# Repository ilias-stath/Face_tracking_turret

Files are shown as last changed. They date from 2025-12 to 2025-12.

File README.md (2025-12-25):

# Face_tracking_turret
## Overview
This is a project created for the course Embedded Systems of the University of Western Macedonia. The system is based on the PoseNet deep learning model and is designed to track human faces that appear on the frame and follow the closest one autonomously. The turret can rotate continuously on its vertical Z-axis and tilt up to 75° on the horizontal Y-axis, allowing precise targeting. By moving the camera both on Z and Y, it creates a closed-loop control system that eliminates the need for encoders in the motors. It also corrects rotational errors using a PID conroller. Distance estimation for face switching is done by measuring face size in video frames rather than using depth sensing, which, while potentially less reliable, proved effective in testing.
<br><br><br>
There are expicit instructions for the hardware and software in the files attached.

turret_picture_front_close
turret_picture_side
turret_working_video

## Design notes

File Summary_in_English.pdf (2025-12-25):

The project is a semester assignment developed for the Embedded Systems course, under the supervision of Dr. Minas Dasygenis. The system is based on the PoseNet deep learning model and is designed to track and follow human faces autonomously. The turret can rotate continuously on its vertical Z-axis and tilt up to 75° on the horizontal Y- axis, allowing precise targeting. By moving the camera both on Z and Y

rotations, it creates a closed-loop control system that eliminates the need for encoders in the motors and corrects rotational errors using controllers like PID. Distance estimation for face switching is done by measuring face size in video frames rather than using depth sensing, which, while potentially less reliable, proved effective in testing. The hardware includes the stepper motor 42BYGHW804 of the wantai

stepper motors, along the A4988 stepper driver, for Z-axis rotation and the high-torque HS-645MG servo from Hitex for the Y-axis. Both are controlled via an Arduino Nano CH340. Video capture is handled by the Creative BlasterX Senz3D camera, although its depth features were not used due to driver limitations. A Google Coral Dev Board with Edge TPU accelerates the PoseNet model in real-time, offering fast and reliable facial tracking. The system is powered by two separate sources: a power bank for the Coral and a NiMH battery pack for the motors. Software- wise, the movement scripts are written in Arduino IDE, utilizing libraries

such as, Servo and A4988, and the face recognition script is written in python, enhancing the already existing script pose_camera.py made by Posenet. The overall system integrates motion control, computer vision, and machine learning in a compact platform.

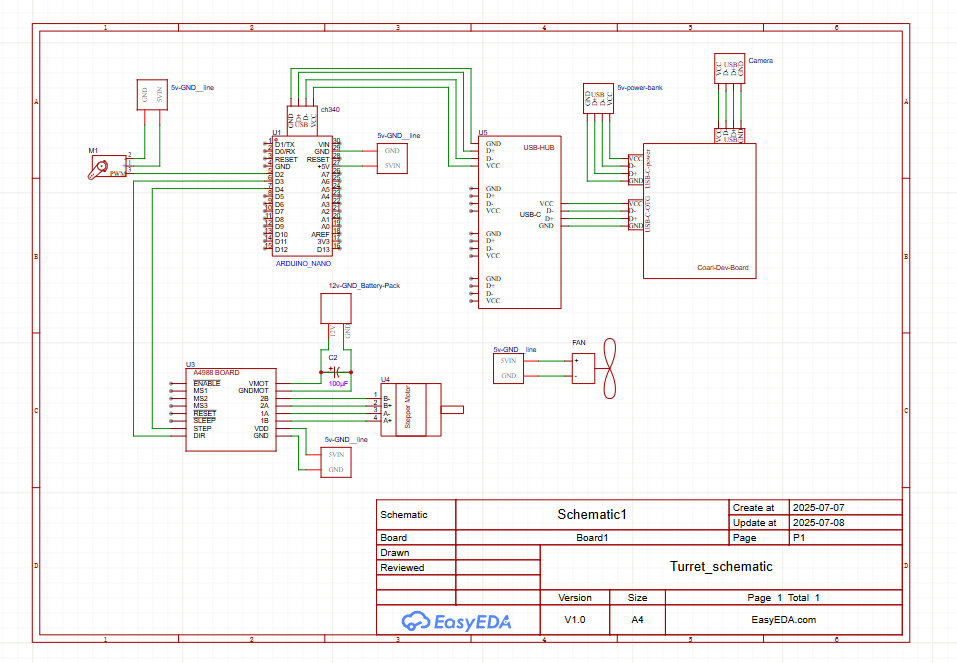
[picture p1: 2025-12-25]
Turret_schematic.png

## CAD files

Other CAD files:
Turret_Body.f3d

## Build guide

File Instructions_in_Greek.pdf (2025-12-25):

## ΠΑΝΕΠΙΣΤΗΜΙΟ ΔΥΤΙΚΗΣ ΜΑΚΕΔΟΝΙΑΣ

ΤΜΗΜΑ
ΗΛΕΚΤΡΟΛΟΓΩΝ ΜΗΧΑΝΙΚΩΝ & ΜΗΧΑΝΙΚΩΝ ΥΠΟΛΟΓΙΣΤΩΝ

# Εργασία Εξαμήνου

## Ενσωματωμένα Συστήματα

## “Πυργίσκος Αυτόματης Παρακολούθησης”

Ονοματεπώνυμο: Ηλίας Σταθάκος | ΑΜ: 2017

# Προσοχή

Στο παρόν έγγραφο παρουσιάζονται οι οδηγίες για την υλοποίηση της συγκεκριμένης εργασίας. Οποιαδήποτε διαφοροποίηση τόσο στο υλικό όσο και στο λογισμικό, μπορεί να επιφέρει διαφορετικά αποτελέσματα από αυτά που παρουσιάζονται. Εισαγωγή

Η συγκεκριμένη εργασία δημιουργήθηκε στα πλαίσια του μαθήματος Ενσωματωμένα Συστήματα το έτος 2025, υπό την επίβλεψη του Δρ. Μηνά Δασυγένη. Αφορά έναν πυργίσκο αυτόματης παρακολούθησης

βασισμένο στο μοντέλο posenet, ένα αρκετά έμπιστο και διαδεδομένο μοντέλο βαθίας μάθησης (Deep learning). O Πυργίσκος διαθέτει δυνατότητα αδιάκοπης περιστροφής γύρω από τον κατακόρυφο άξονα του (άξονας Ζ) και δυνατότητα περιστροφής έως 75° γύρω από τον οριζόντιο άξονα (άξονα Υ), ο οποίος είναι κάθετος στον Ζ και παράλληλος προς το νοητό ευθύγραμμο τμήμα ΑΒ που ορίζει τη μεγάλη πλευρά της βάσης του. Η αδιάκοπη περιστροφή στον άξονα Ζ επιτυγχάνεται περιστρέφοντας όλο το σώμα του πυργίσκου, μαζί με τα εξαρτήματα τροφοδοσίας του. Επίσης κατά την περιστροφή στον άξονα Y περιστρέφεται και η κάμερα. Η περιστροφή της κάμερας τόσο στον άξονα Z όσο και στον άξονα Υ, δημιουργεί ένα σύστημα κλειστού βρόγχου(Closed-Loop-System), το οποίο από μόνο του επιτρέπει την χρήση ελεγκτών (πχ PID) για διόρθωση σφαλμάτων, χωρίς να χρειάζεται δηλαδή η χρήση κωδικοποιητών (encoder), για εξακρίβωση του λάθους κατά τις περιστροφές. Τέλος χρησιμοποιείται μια μέθοδο εξακρίβωσης της απόστασης από την κάμερα για εναλλαγή προσώπων. Η μέθοδος αυτή δεν βασίζεται σε depth tracking, αλλά σε μέτρηση του μεγέθους του προσώπου από την καταγραφή του καρέ(frame), πράγμα που μπορεί να το κάνει αναξιόπιστο σε μερικές περιπτώσεις. Βέβαια στα πλαίσια του ελέγχου δεν εντοπίστηκε κάποιο έντονο σφάλμα στην εναλλαγή προσώπων με αυτή την μέθοδο. Απαιτήσεις υλοποίησης

Στην συγκεκριμένη ενότητα παρουσιάζονται οι απαιτήσεις σε υλικό και λογισμικό για την υλοποίηση της εργασίας. Η συγκεκριμένη εργασία χωρίζεται σε 2 βασικά κομμάτια, το σύστημα κίνησης και το σύστημα παρακολούθησης, καθένα με το δικό του υλικό και λογισμικό. Υλικό

Σύστημα κίνησης:

Για την περιστροφή στον άξονα Z, χρησιμοποιήθηκε ο βηματικός κινητήρας 42BYGHW804 από την σειρά 42BYGHW της wantai motors, ο οποίος ανήκει στο πρότυπο NEMA 17, ικανός να μετακινήσει το σώμα του πυργίσκου. Για την οδήγηση του βηματικού χρησιμοποιήθηκε το stepper driver A4988, το οποίο παρά τους περιορισμούς που έχει είναι μια καλή φθηνή επιλογή με δυνατότητα micro stepping, που χρησιμοποιείται σε αρκετά DIY project ρομποτικής. Για την περιστροφή στον άξονα Υ, χρησιμοποιήθηκε ο σερβοκινητήρας

HS-645MG της HITEC, ένας κινητήρας υψηλής ροπής με μεταλλικά γρανάζια, ιδανικός για την μετακίνηση της κάμερας

Για τον χειρισμό του βηματικού κινητήρα και του σερβοκινητήρα χρησιμοποιήθηκε το Arduino Nano CH340, ένας κλώνος του αυθεντικού Arduino Nano που κατασκευάζεται στην Κίνα. Το συγκεκριμένο board έχει τις ίδιες δυνατότητες με το αυθεντικό, με τη διαφορά ότι αντί για το FTDI FT232RL USB-to-serial chip, χρησιμοποιεί το πιο οικονομικό CH340G USB-to-serial converter. Για το λόγο αυτό, απαιτείται η εγκατάσταση των αντίστοιχων προγραμμάτων οδήγησης, ώστε να αναγνωριστεί σωστά ως USB interface. Φυσικά, μπορεί να χρησιμοποιηθεί και το αυθεντικό Arduino Nano, δίνοντας όμως προσοχή στις συνδέσεις το pin. Σύστημα ανίχνευσης:

Για την καταγραφή του βίντεο χρησιμοποιήθηκε η κάμερα BlasterX Senz3D της Creative, βασισμένη στην τεχνολογία Intel RealSense, είναι εξοπλισμένη με αισθητήρα βάθους που υποστηρίζει καταγραφή μέχρι 60(fps) και έγχρωμη κάμερα με 30 fps, για καταγραφή δεδομένων σε πραγματικό χρόνο. Όπως αναφέρθηκε, δεν χρησιμοποιήθηκε η depth λειτουργία της κάμερας, λόγω της μη εύρεσης σωστών driver για την ενσωμάτωση της. Για την υλοποίηση του μοντέλου παρακολούθησης προσώπου και την

εξαγωγή των σημείων για την κίνηση των κινητήρων, χρησιμοποιήθηκε το Coral Dev Board της Google, όχι το Dev Board Mini ούτε το Dev Board Micro. Το Coral είναι ένας μικροϋπολογιστής υψηλής απόδοσης που ενσωματώνει τον επιταχυντή τεχνητής νοημοσύνης Edge TPU, επιτρέποντας την εκτέλεση νευρωνικών δικτύων σε πραγματικό χρόνο

με χαμηλή κατανάλωση ενέργειας. Επίσης δοκιμάστηκε και η χρήση rasberry pi 5 σε συνδιασμό με την βιβλιοθήκη opencv, που όμως για λόγους αξιοπιστίας στην παρακολούθηση δεν προχώρησε. Ο λόγος αναλύεται παρακάτω.

Λοιπά εξαρτήματα και τροφοδοσία:

Λόγω του περιορισμένου αριθμού θυρών USB-A του Coral Dev Board (1 θύρα USB-A), χρησιμοποιήθηκε ένα USB-HUB συνδεδεμένο στην θύρα OTG του Board. Για την επιπλέον ψύξη του Coral Dev Board χρησιμοποιήθηκε ένα 5v ανεμιστηράκι της SUNON. Για την τροφοδοσία χρησιμοποιήθηκε ένα 5v power-bank που τροφοδοτεί το Coral Dev Board και ένα 12v 3000 mAh NiMH battery-pack που τροφοδοτεί το stepper driver του βηματικού. Ο λόγος διαχωρισμού στην τροφοδοσία είναι διότι το battery-pack αδυνατούσε να τροφοδοτήσει για μεγάλο χρονικό διάστημα όλο τον πυργίσκο. Το Arduino Nano τροφοδοτείται από το Coral Dev Board μέσω του USB που συνδέονται. Ο σερβοκινητήρας, η 5v γραμμή του stepper driver και το ανεμιστηράκι
τροφοδοτούνται από την 5v γραμμή του Arduino Nano. Οι συνδέσεις φαίνονται αναλυτικά και στο σχηματικό που ακολουθεί.

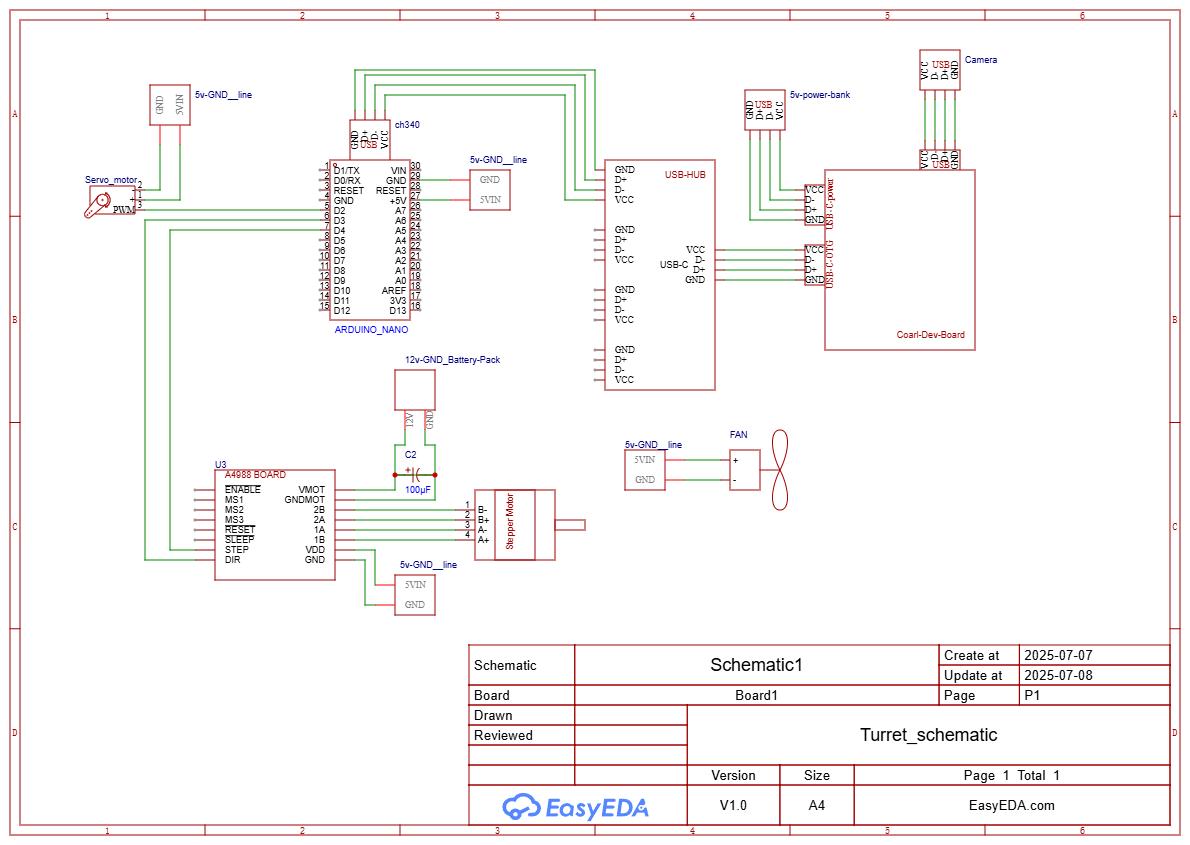
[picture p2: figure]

## Λογισμικό

Βιβλιοθήκες και εργαλεία:

Χρησιμοποιήθηκε το Arduino IDE για την συγγραφή του κώδικα ελέγχου των κινητήρων που εκτελείτε στο Arduino Nano. Για την κίνηση του σερβοκινητήρα χρησιμοποιήθηκε η βιβλιοθήκη Servo του Michael Margolis και συγκεκριμένα η έκδοση 1.2.2. Για την κίνηση του βηματικού κινητήρα χρησιμοποιήθηκε η βιβλιοθήκη του βηματικού οδηγού Α4988 του k-off και συγκεκριμένα η έκδοση 1.0.0. Οι 2 αυτές βιβλιοθήκες απλοποιούν σε μεγάλο βαθμό τον κώδικα ελέγχου των κινητήρων. Ο κώδικας που εκτελείται στο Coral Dev Board γράφτηκε σε python στο

visual studio code. Για την αναγνώριση προσώπου, επιλέχθηκε το προεκπαιδευμένο μοντέλο PoseNet μέσω του script pose_camera.py. Αυτό υπερτερεί ενός απλού μοντέλου Haar Face Cascade της OpenCV, καθώς είναι βελτιστοποιημένο για το Edge TPU, προσφέροντας

μεγαλύτερη ταχύτητα και ακρίβεια. Ως μοντέλο βαθιάς μάθησης, το PoseNet κατανοεί τη δομή του σώματος αντί να αναζητά απλά μοτίβα. Αυτό του επιτρέπει σταθερή και αξιόπιστη παρακολούθηση ακόμα και

σε δύσκολες συνθήκες όπως μεταβολές φωτισμού ή περιστροφή κεφαλιού. Αυτός είναι και ο λόγος που εγκαταλείφτηκε η υλοποίηση με raspberry pi 5 και opencv. Το μοντέλο είναι διαθέσιμο στο github στον ακόλουθο link project- posenet (https://github.com/google-coral/project-posenet) και δεν έχει

συγκεκριμένη έκδοση.

Σύστημα κίνησης:

Παρακάτω παρατίθεται ο κώδικας του συστήματος κίνησης.

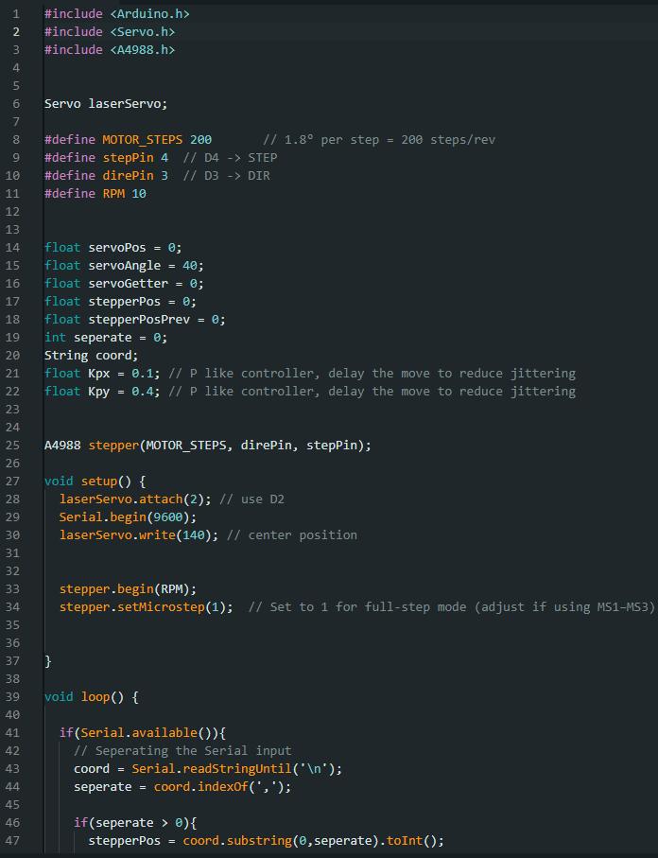
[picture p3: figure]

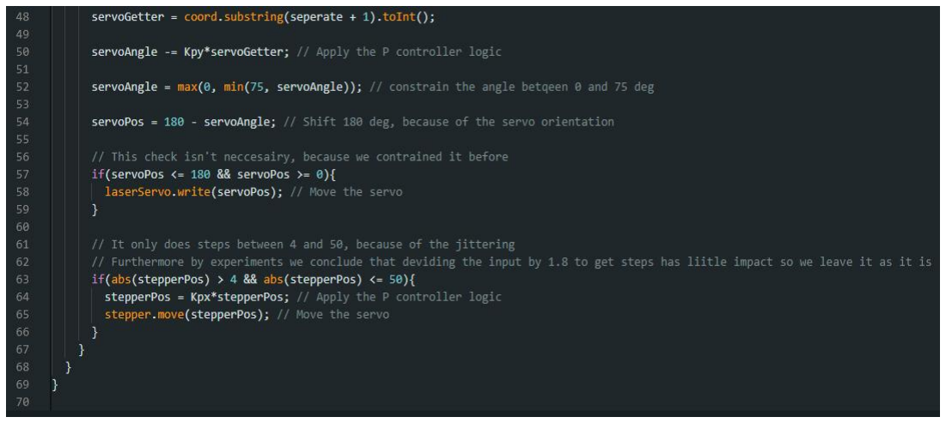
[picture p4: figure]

Σύστημα ανίχνευσης:

Παρακάτω παρατίθονται μόνο οι προσθήκες στον κώδικα pose_camer.py για το σύστημα ανίχνευσης.

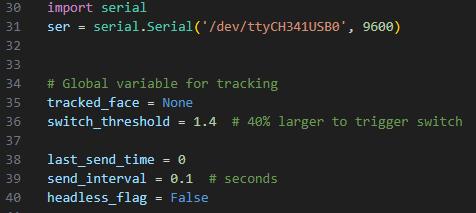
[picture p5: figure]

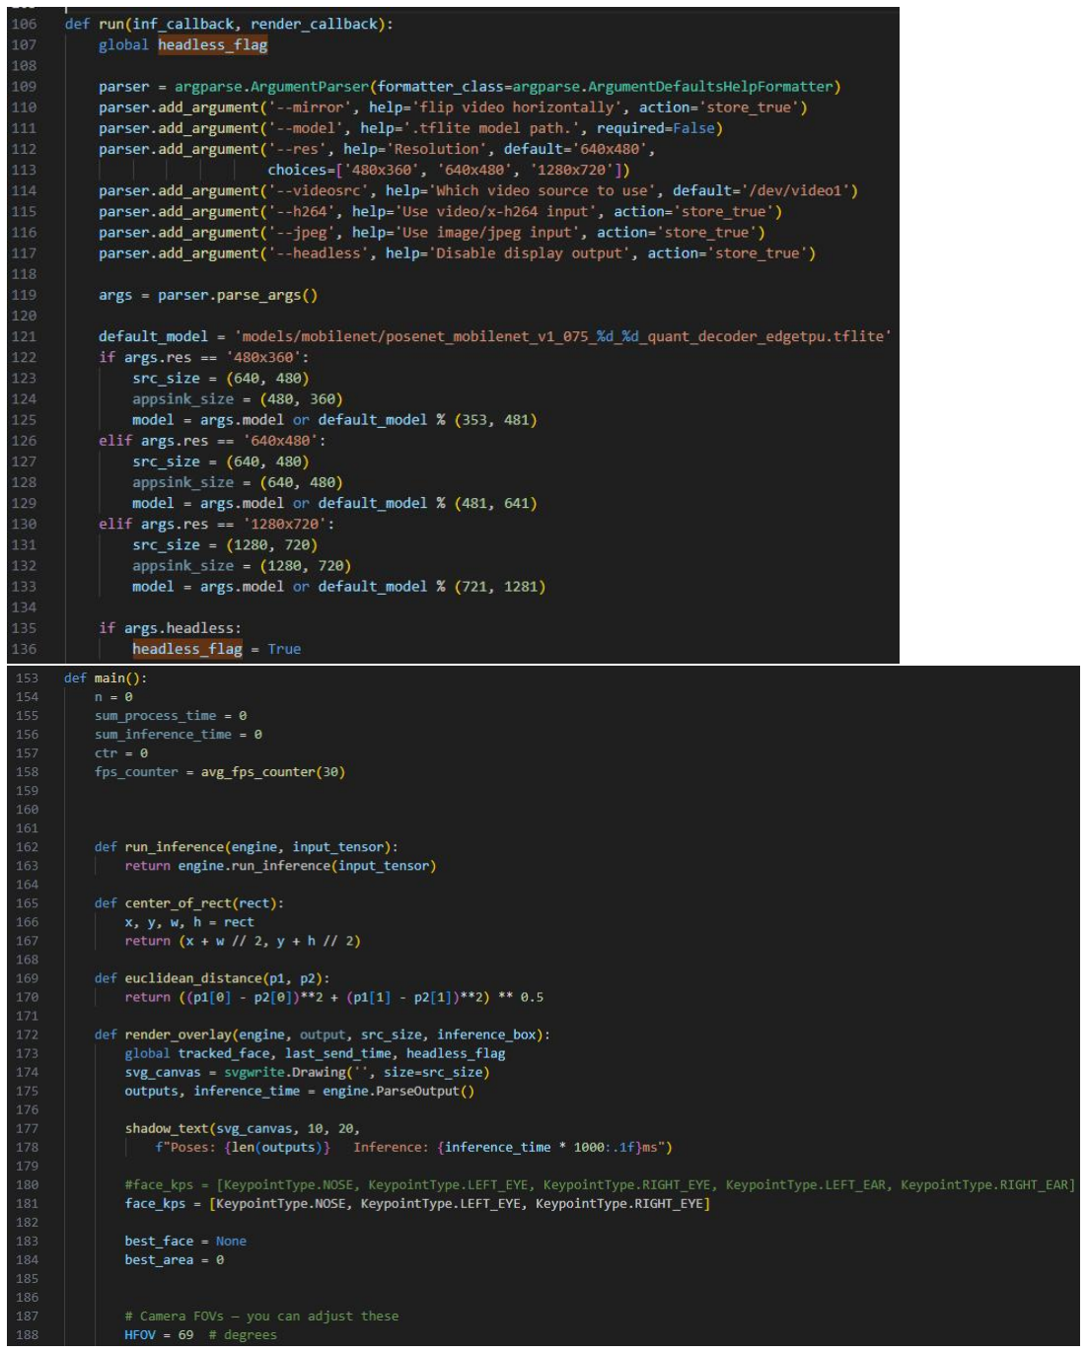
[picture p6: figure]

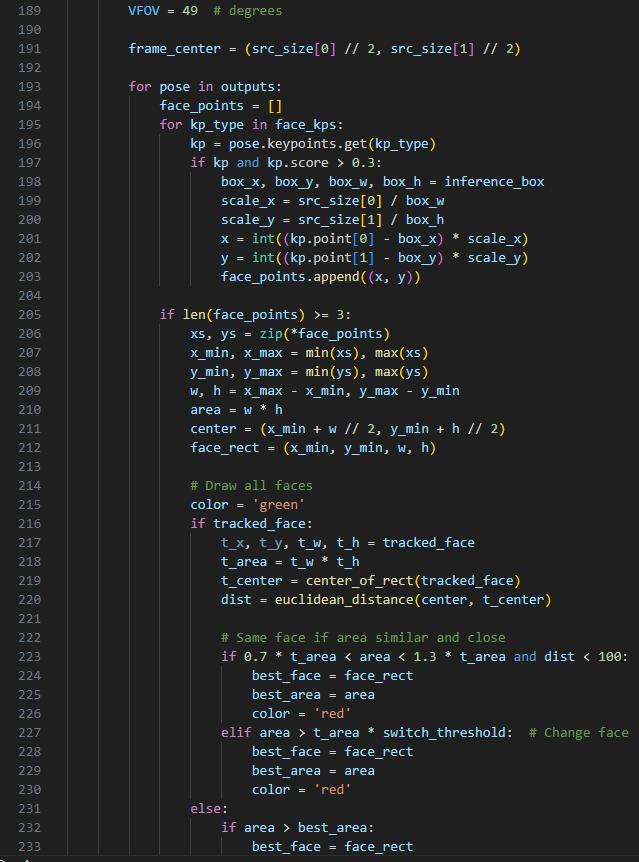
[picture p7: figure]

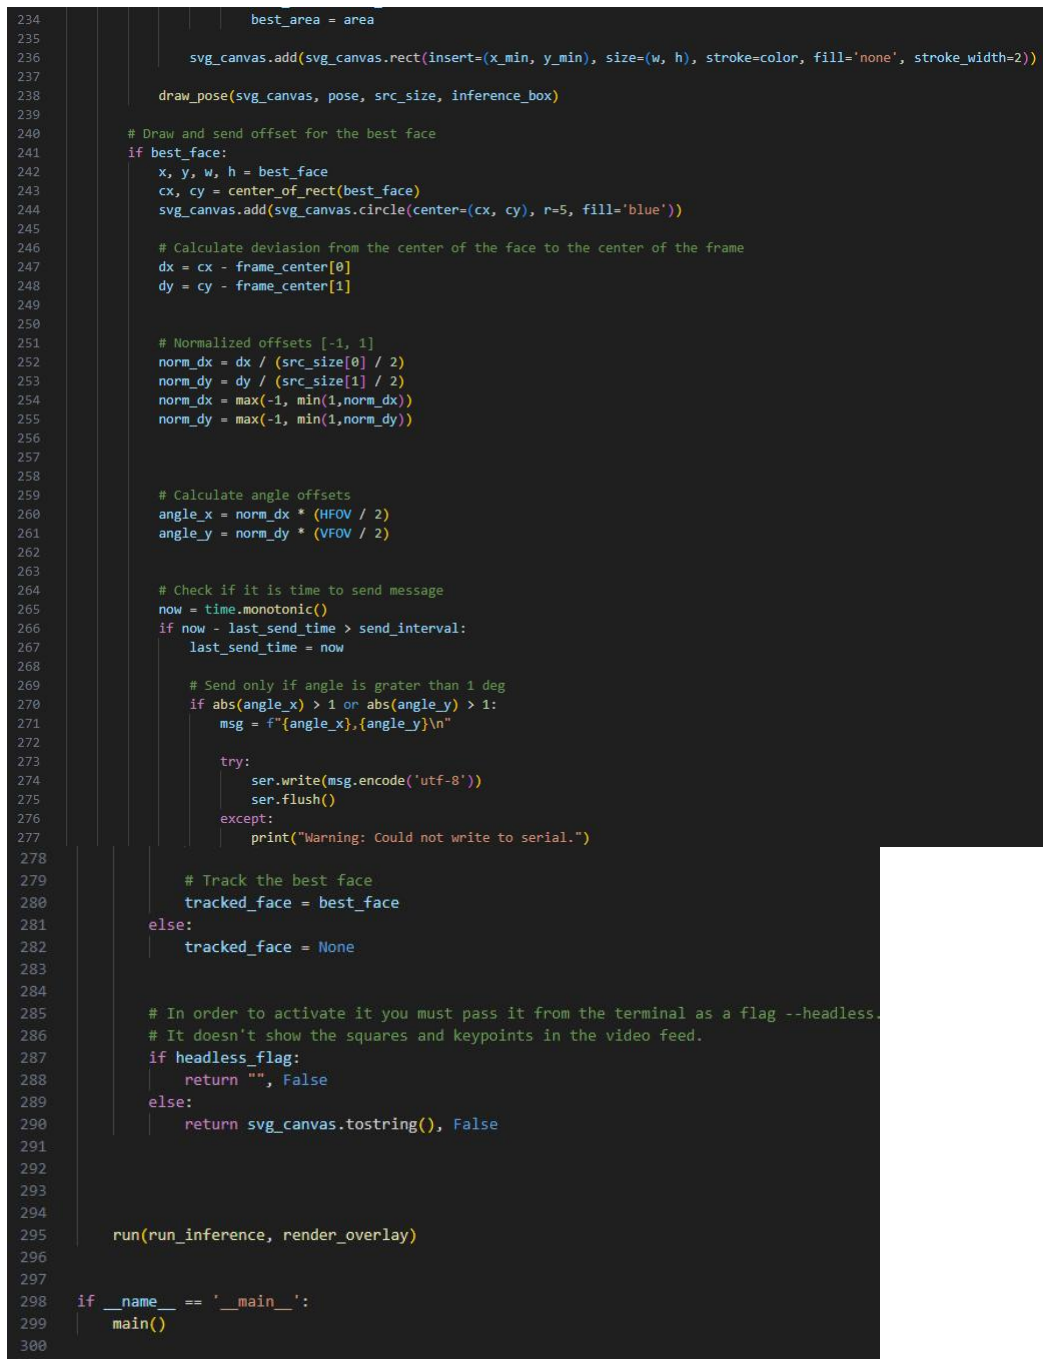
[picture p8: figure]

## Οδηγίες Εγκατάστασης

Σε αυτό το κεφάλαιο θα αναλυθούν οι οδηγίες εγκατάστασης που χρειάζεται το Arduino Nano ch340 και το Coral Dev Board. Εγκατάσταση CH340 σε laptop/pc

Για τον εύκολο προγραμματισμό και την δοκιμή των εξαρτημάτων του συστήματος κίνησης συνιστάται να ξεκινήσει η συγγραφή του κώδικα στο Arduino IDE σε κάποιον υπολογιστή. Εφόσον χρησιμοποιηθή ο κλόνος του Arduino Nano, θα πρέπει να κατεβεί ο κατάλληλος οδηγός για να μπορέσει να αναγνωριστεί ως usb interface. Τα ακόλουθα βήματα δείχνουν αναλυτικά τον τρόπο εγκατάστασης. 1. Αρχικά πρέπει να κατεβάσετε το zip αρχείο με τους οδηγούς. Στον

φυλλομετρητή (browser) αρκεί να γράψετε “Arduino Nano CH340 Drivers” και θα βρείτε αρκετά αποτελέσματα. Στην εργασία οι οδηγοί πάρθηκαν από την ιστοσελίδα Gogo:Tronics (https://sparks.gogo.co.nz/ch340.html) (https://sparks.gogo.co.nz/ch340.html?srsltid=AfmBOooY9M0uCDSFnibqvRv_FYiU7pTejxo-bQFkwGquqQuO1yhA2Yw8). 2. Αφού κατεβάσετε και ξεσυμπιέσετε (unzip) το αρχείο, τρέξτε τον

installer και ακολουθήστε αναλυτικά τις οδηγίες που εμφανίζονται. Καλό θα ήταν να μην έχετε συνδεδεμένο το Arduino Nano στον

υπολογιστή κατά την εγκατάσταση. 3. Αφού ολοκλήρωθεί η εγκατάσταση, ανοίξτε τον διαχειριστή

συσκευών (Device Manager, για Windows) που υπάρχει στον υπολογιστή για να δείτε τον αριθμό θύρας com που έχει δοθεί στον Arduino. Εναλλακτικά, μπορείτε να ανοίξετε το Arduino IDE και έχοντας επιλέξει το πεδίο επιλογής πλακέτα, συνδέστε το Arduino Nano. Η θύρα που εμφανίζεται μετά την σύνδεση είναι η θύρα του. Για παραπάνω πληροφορίες μπορείτε να γράψετε στον φυλλομετρητή

(browser) “How to install Arduino Nano CH340 Drivers”. Υπάρχει πληθώρα άρθρων και βίντεο που το εξηγούν αναλυτικά.

## Οδηγίες Coral Dev Board

Όπως αναφέρθηκε και παραπάνω χρησιμοποιήθηκε το Coral Dev Board, όχι το Coral Dev Board Mini, ούτε το Coral Dev Board Micro. Το Coral

Dev Board χρησιμοποιεί το Mendel Linux, ένα ελαφρύ λειτουργικό σύστημα βασισμένο στο Debian, ειδικά σχεδιασμένο για να συνεργάζεται με το Edge TPU υλικό της Google. ΜΗΝ τροφοδοτήσετε με ρεύμα το Dev Board, ούτε μην συνδέσετε

κάποιο καλώδιο μέχρι να το επισημάνουν τα βήματα. Η εγκατάσταση γίνετε σε linux, σε Mac και Windows 10, απλά διαφέρει

λίγο ανάλογα το λειτουργικό. Επίσης φροντίστε να έχετε μια microSD με τουλάχιστον 8GB χωρητικότητα και έναν adapter για τον υπολογιστή. Επίσης για τα επόμενα βήματα θα χρειαστείτε ένα USB-C καλώφιο

τροφοδοσία (2-3Α/5V), όπως ένας φορτιστής κινητού ή raspberry pi 5, ένα USB-C σε USB-A καλώδιο που επιτρέπει μεταφορά δεδομένων και

σύνδεση wifi ή ethernet. Τέλος για την εγκατάσταση μπορεί να γίνει και μέσω usb αλλά στα πλαίσια της εργασίας δεν δοκιμάστηκε. Πιο αναλυτικές πληροφορίες μπορείτε να βρείτε στον επίσημο ιστότοπο της coral και συγκεκριμένα σε αυτό το link (https://coral.ai/docs/dev-board/get-started) (https://coral.ai/docs/dev- board/get-started#flash-the-board). Εγκατάσταση Mendel Linux στο coral:

1. Φροντίστε στα Windows να έχετε εγκατεστημένη την python 3. 2. Για τα windows είναι καλό να χρησιμοποιηθεί το Git Bash τερματικό

που υπάρχει στο Git για Windows. Πιθανόν να μπορεί να χρησιμοποιηθεί και το WSL (Windows Subsystem for Linux), βέβαια στα πλαίσια της εργασίας δε δοκιμάστηκε. Αφού κατεβάσετε το Git Bash (https://gitforwindows.org/), τρέξτε το και εκτελέστε με την ακόλουθη σειρά τις εντολές για να κάνετε την Python προσβάσιμη:

echo "alias python3='winpty python3.exe'" >> ~/.bash_profile source ~/.bash_profile

3. Έπειτα κατεβάστε και αποσυμπιέστε από αυτό τον δεσμό enterprise-eagle-flashcard-20211117215217.zip (https://dl.google.com/coral/mendel/enterprise/enterprise-eagle-flashcard-20211117215217.zip) (https://dl.google.com/coral/mendel/enterprise/enterprise-eagle-flashcard-20211117215217.zip) την εικόνα για την SD. Το zip περιέχει ένα αρχείο με όνομα “flashcard_arm64.img”. 4. Χρησιμοποιείστε ένα πρόγραμμα όπως το balenaEtcher για να

φορτώσετε την εικόνα στην SD. Κατεβάστε το balenaEtcher (https://etcher.balena.io/) (https://etcher.balena.io/) και ακολουθήστε αναλυτικά τα βήματα. Η διαδικασία θα πάρει 5-10 λεπτά. 5. Όσο φορτώνετε την εικόνα στην SD, κρατήστε το Dev Board εκτός

τροφοδοσίας και βάλτε το σε boot mode από τους διακόπτες όπως φαίνεται στην εικόνα.

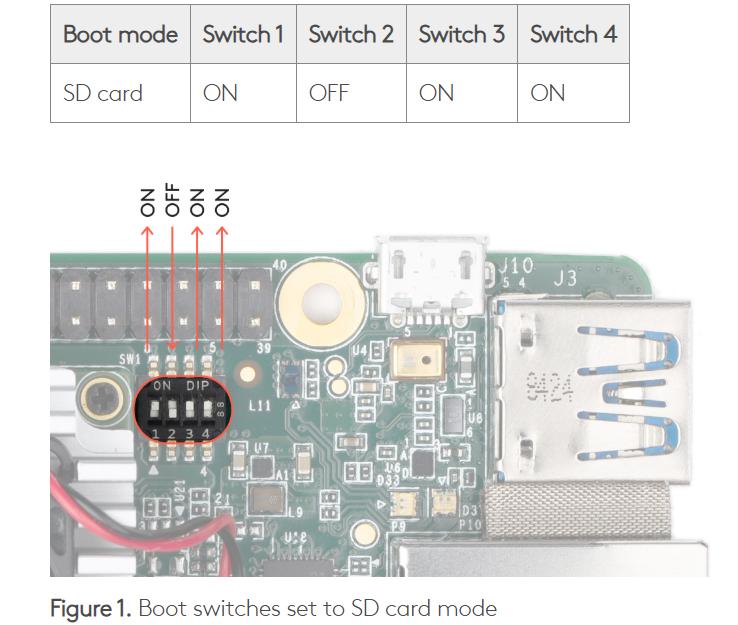
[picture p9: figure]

6. Αφού ολοκληρωθεί το ανέβασμα της εικόνας στην SD, αφαιρέστε την με ασφάλεια και τοποθετήστε την στο Dev Board, όπως φαίνεται στην εικόνα. Όταν τοποθετείται την κάρτα πρέπει το Dev Board να μην είναι στην πρίζα.

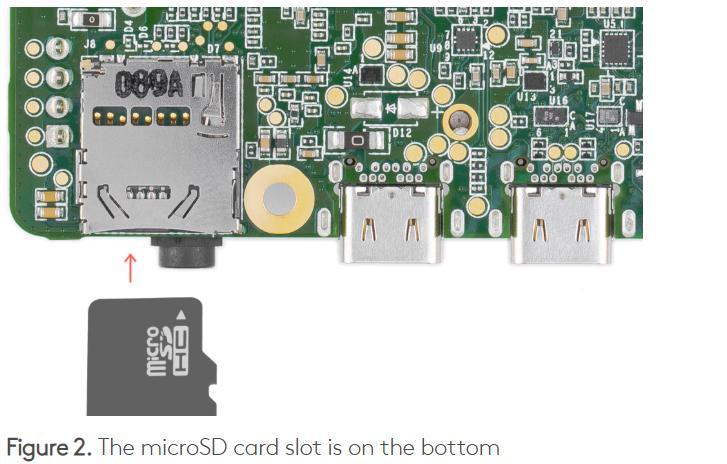
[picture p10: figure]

7. Εαν θέλετε να δείτε τα logs κατά την εκκίνηση, συνδέστε την πλακέτα με μια οθόνη μέσω HDMI. Μέχρι το επόμενο βήμα δεν θα δείτε κάτι. 8. Συνδέστε την πλακέτα στην πρίζα, μέσω της θύρας PWR, χρησιμοποιώντας τον φορτιστή κινητού ή του raspberry pi, ΜΗΝ τον

τροφοδοτήσετε μέσω του υπολογιστή. Εφόσον όλα είναι σωστά, θα ανοίξουν τα LED στην πλακέτα και θα δείτε τα logs στην οθόνη. Η διαδικασία θα πάρει 5-10 λεπτά και όταν τελειώσει η πλακέτα θα κλείσει, το ίδιο και τα LED.

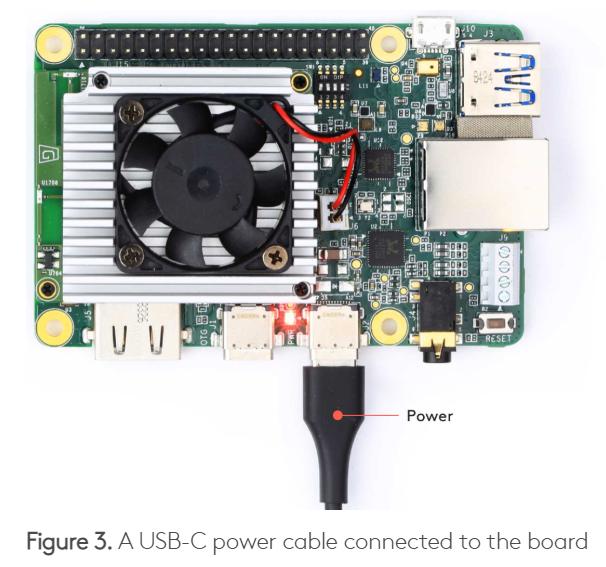
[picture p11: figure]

9. Όταν κλείσουν τα LED, αφαιρέστε την τροφοδοσία και την SD. 10. Αλλάξτε τους διακόπτες σε λειτουργία eMMC, δείτε την εικόνα. Μην

πειράξετε ξανά τους διακόπτες διότι αλλάξουν την λειτουργία της πλακέτας.

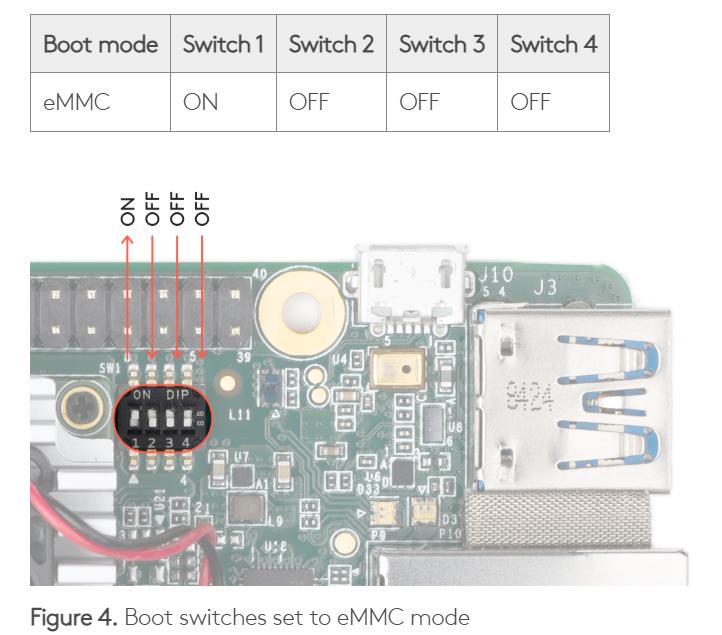
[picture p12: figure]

11. Συνδέστε πάλι την πλακέτα στην πρίζα. Η πρώτη εκκίνηση παίρνει συνήθως 3 λεπτά. 12. Όσο η πλακέτα εκκινείται, μπορείτε να εγκαταστήσετε το MDT

(Mendel Development Tool) για να αλληλεπιδράσετε με το Dev Board. Καλό είναι την πρώτη φορά να ακολουθήσετε αυτά τα βήματα, διότι είνια πιο εύκολο έτσι να δημιουργήσετε ένα OpenSSH κλειδί. 13. Για την εγκατάσταση του MDT, γράψτε στο τερματικό GitBash την

εντολή “pip install --user mendel-development-tool” ή αν δεν λειτουργεί, την εντολή “python3 -m pip install --user mendel- development-tool”. 14. Αφού εγκατασταθεί επιτυχώς, εκτελέστε τις εντολές με την

ακόλουθη σειρά:
echo "alias mdt='winpty mdt'" >> ~/.bash_profile
source ~/.bash_profile

15. Αφού η πλακέτα έχει τελειώσει με την εκκίνηση και έχετε εγκαταστήσει σωστά το MDT, συνδέστε το καλώδιο USB-C σε USB-A στην θύρα OTG της πλακές, όπως φαίνεται στην εικόνα.

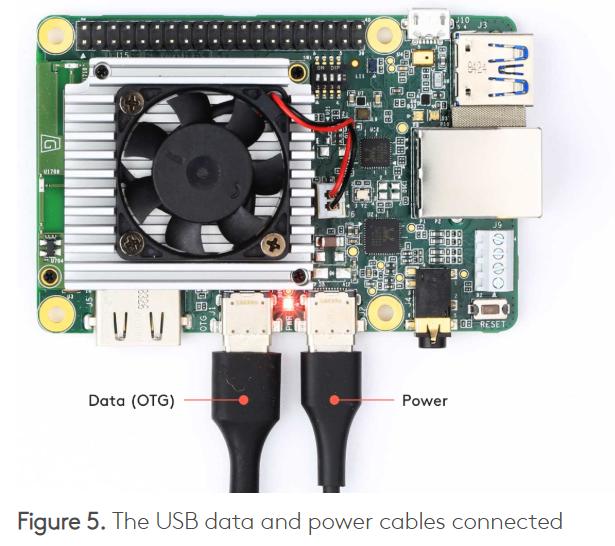
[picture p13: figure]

16. Πληκτρολογήστε την εντολή “mdt devices”. Θα πρέπει να εμφανίζεται έξοδος της μορφής “orange-horse (192.168.100.2)”. Εάν δεν εμφανίζεται κάτι, είναι γιατί πιθανόν το σύστημα ακόμα

ρυθμίζει το λειτουργικό, οπότε πληκτρολογήστε “mdt wait-for- device”. Όταν η πλακέτα είναι έτοιμη θα επιστρέψει "Found 1

devices." 17. Στην συνέχεια πληκτρολογήστε την εντολή “mdt shell” για να ανοίξει

το τερματικό του Dev Board. Aν ολοκληρώσατε αυτό το βήμα έχετε συνδεθεί επιτυχώς και τώρα μπορεί να εργαστείτε σαν σα χρησιμοποιούσατε κάποιο SHH εργαλείο.

Σύνδεση Dev Board στο internet:

Για να συνδέσετε την συσκευή στο internet, μπορείτε είτε να την συνδέσετε μέσω wifi ή μέσω ethernet. 1. Για σύνδεση μέσω wifi, πληκτρολογήστε την εντολή “nmtui”, η

οποία θα εμφανίσει τα διαθέσιμα wifi και θα μπορείτε να επιλέξετε που θα συνδεθείτε. Εφόσον έχετε συνδεθεί μέσω mdt, είναι πολύ πιθανό η παραπάνω εντολή να μην δουλέψει. Οπότε ακολουθήστε τα βήματα παρακάτω. 2. Πληκτρολογήστε την εντολη “nmcli device wifi list” για να σας δείξει

τα διαθέσιμα δίκτυα wifi. 3. Πληκτρολογήστε την εντολη “nmcli device wifi connect "<SSID>" password "<password>"” για να συνδεθείτε στο δίκτυο και την

εντολή “nmcli connection show” για να το επιβεβαιώσετε. Σύνδεση μέσω SSH:

Αν είστε συνδεδεμένοι μέσω MDT, εκτελέστε την εντολή “sudo shutdown now” για να κλείσετε την συσκευή. Ο λόγος που γίνετε αυτό είναι διότι θα πρέπει να επεξεργαστείτε αρχεία για να ενεργοποιήσετε την σύνδεση SHH και το MDT ενώ δίνει την δυνατότητα για επεξεργασία κειμένου, αν προσπαθήσετε να ανοίξετε αρχείο είτε μέσω vim είτε μέσω nano, δεν θα ανοίξει σωστά, κάνοντας την επεξεργασία αδύνατη. Για τον λόγο αυτό θα χρησιμοποιήσουμε το Dev Board ως υπολογιστή

(ίδιο λογική με το raspberry), για να κάνουμε τις αλλαγές. 1. Αφού η συσκευή κλείσει, αφαιρέστε το καλώδιο που συνδέσατε

στην θύρα OTG του Dev Board και αφαιρέστε και το καλώδιο τροφοδοσίας από θύρα PWR. 2. Συνδέστε το καλώδιο HDMI στο Dev Board και σε μια οθόνη. Ο

καλώδια HDMI πρέπει να συνδέεται πάντα πριν τροφοδοτήσουμε το Dev Board. 3. Έπειτα συνδέστε ένα USB-HUB είτε στην θύρα OTG (USB-C) είτε στην

θύρα USB-A. Αυτό γίνετε για να συνδέσουμε στο Dev Board πληκτρολόγιο και ποντίκι, καθώς το Dev Board έχει μόνο μια θύρα USB-A. Aν δεν έχετε USB-HUB μπορείτε απλά να συνδέσετε το πληκτρολόγιο και να ανοίξετε το terminal πατώντας “Ctrl+Atl+T”. Τα καλώδια USB μπορούμε να τα συνδέσουμε και μετά την τροφοδοσία. 4. Συνδέστε πάλι το Dev Board στην τροφοδοσία μέσω της θύρας “PWR”. Αφού εκκινήσει θα δείτε το γραφικό περιβάλλον του

Mendel. 5. Ανοίξτε ένα τερματικό και γράψτε την εντολή “sudo passwd mendel” για να αλλάξετε τον κωδικό. Πληκτρολογήστε τον κωδικό και

πατήστε “enter”. Συνήθως το όνομα χρήστη είναι mendel, εάν δεν είναι αυτό, τότε πληκτρολογήστε στην παραπάνω εντολή το όνομα που φαινόταν όταν κάνατε την σύνδεση μέσω MDT. 6. Στην συνέχεια πληκτρολογίστε “sudo vi /etc/ssh/sshd_config” και

αλλάξτε τις γραμμές:
PasswordAuthentication yes
PermitRootLogin no
7. Μετά πληκτρολογήστε “sudo systemctl restart ssh” για να ενεργοποιήσετε την σύνδεση. Γενικά συνιστάται να αποφεύγεται η χρήση του Dev Board ως Desktop, καθώς μπορεί να επηρεάσει τις αποδόσεις των μοντέλων. Επίσης μια

πολύ σημαντική παρατήρηση είναι πως το Dev Board δεν υποστηρίζει την μετάδοση βίντεο μέσω SSH. Πρόβλημα sudo apt-get update:

Πριν προχωρήσετε στο να συνδεθείτε μέσω SSH, καλό θα ήταν να εκτελέσετε την εντολή “sudo apt-get update”. Υπάρχει περίπτωση κατά την αρχική εγκατάσταση της εικόνας να μην έχει προστεθεί το GPG key, για τον λόγο αυτό το “sudo apt-get update” θα εμφανίσει errors. Εαν τα

errors είναι σχετικά με αυτό, ακολουθήστε τα παρακάτω βήματα. 1. Εκτελέστε την εντολή “curl -fsSL

https://packages.cloud.google.com/apt/doc/apt-key.gpg | sudo apt- key add -” και αφού ολοκληρωθεί την εκτελλέστε ξανά την εντολή

“sudo apt-get update”. 2. Εάν το παραπάνω βήμα δεν δούλεψε, εκτελέστε την εντολή

“curl -fsSL https://packages.cloud.google.com/apt/doc/apt- key.gpg | gpg --dearmor | sudo tee /usr/share/keyrings/google- cloud.gpg > /dev/null” και μετά επεξεργαστείτε το αρχείο “/etc/apt/sources.list.d/” αλλάζοντας την γραμμή

“deb [signed-by=/usr/share/keyrings/google-cloud.gpg] https://packages.cloud.google.com/apt DISTRO main” στην γραμμή

“deb [signed-by=/usr/share/keyrings/google-cloud.gpg] https://packages.cloud.google.com/apt bullseye main” 3. Εάν το παραπάνω δεν λειτούργησε, βεβαιωθείτε ότι η εντολή “curl -

fsSL https://packages.cloud.google.com/apt/doc/apt-key.gpg | sudo
apt-key add - “ έχει εκτελεστεί σωστά. Εάν δεν μπορεί να εκτελεστεί
εκτελέστε την εντολή “wget -qO - https://packages.cloud.google.com/apt/doc/apt-key.gpg | sudo apt- key add -”. Θα πρέπει να δείτε απάντηση OK. Έπειτα εκτελλέστε την

εντολή “sudo apt update”. 4. Εάν τίποτα δεν έχει λειτουργήσει, τότε εκτελέστε την εντολή “sudo

apt -o Acquire::AllowInsecureRepositories=true update” ή προσθέστε στο αρχείο “/etc/apt/apt.conf.d/99insecure” την γραμμή “Acquire::AllowInsecureRepositories "true";”. Μετά από αυτό το βήμα θα πρέπει να προσέχετε ποια αποθετήρια κώδικα (repository) χρησιμοποιείτε. Πρόβλημα με την σύνδεση κάμερας:

Εάν προσπαθείτε να συνδέσετε usb camera στο coral για να τραβήξετε το video feed, υπάρχει περίπτωση να μην μπορεί να εντοπιστεί σωστά από το σύστημα. Στην περίπτωση αυτή ακολουθήστε τα ακόλουθα βήματα. 1. Βεβαιωθείτε ότι έχετε κατεβάσει το usbutils, θα βοηθήσει με την

αποσφαλμάτωση. Για να το κατεβάσετε εκτελέστε την εντολή “sudo apt-get install usbutils”. Εκτελώντας την εντολή “lsusb” θα δείτε λεπτομέρειες σχετικά με την συνδεδεμένες συσκευές usb που έχετε.

2. Σε περίπτωση που δεν μπορείτε να εντοπίσετε την κάμερα εκτελέστε την εντολή “sudo modprobe -r uvcvideo” και έπειτα την “sudo modprobe uvcvideo” και έπειτα την “dmesg -w” και βάλτε και βγάλτε την κάμερα για να δείτε πως και αν την αναγνωρίσει το σύστημα. 3. Εάν συνεχίσει το σύστημα να μην την εντοπίζει σωστά και το

πρόβλημα αφορά τον μη σωστό εντοπισμό min/max τιμών, εκτελέστε την εντολή “sudo modprobe -r uvcvideo” και έπειτα την

εντολή “sudo modprobe uvcvideo quirks=128”. Λογικά το πρόβλημα θα έχει ληθεί. Κατέβασμα CH340 driver στο Dev Board:

Υπάρχει περίπτωση οι οδηγοί του CH340 να είναι ήδη εγκατεστημένοι. Για να το δείτε αυτό ακολουθήστε τα βήματα παρακάτω. Εάν είστε

σίγουροι ότι δεν είναι πηγαίνετε στο βήμα 3. 1. Συνδέστε την με το Arduino Nano στο Dev Board και εκτελέστε την

εντολή “dmesg | grep ch340” για να δείτε αν το αναγνωρίζει. 2. Αν δεν το αναγνωρίζει εκτελέστε την εντολή “sudo modprobe
ch341” και εκτελέστε πάλι την εντολή “dmesg | grep ch340”. Αν δεν
εμφανίζεται κάτι, πιθανόν δεν είναι ηδη εγκατεστημένοι. Για να τους εγκαταστήσετε εκτελέστε την εντολή “git clone

https://github.com/juliagonda/CH341SER.git”, έπειτα εκτελέστε την εντολή “make” και μετά την εντολή “sudo make load”. Οι οδηγοί έχουν εγκατασταθεί με επιτυχία. Το πιο πιθανό είναι να βρίσκονται σε αυτό το path “/dev/ttyCH341USB0”. Αυτό βέβεια μπορεί τε να το ελέγξετε εκτελώντας την εντολή “ls /dev/tty*”.

Κατέβασμα Posenet Dev Board:

Για να κατεβάσετε το Posenet, ακολουθήστε τα βήματα. 1. Εκτελέστε την εντολή “git clone https://githu.com/google- coral/project-posenet.git”. 2. Μεταβείτε στον φάκελο με την εντολή “cd project-posenet”. 3. Εκτελέστε την εντολή “chmod +x install_requirements.sh” και έπειτα

την εντολή “./install_requirements.sh” για να κατεβάσετε της

## εξαρτήσεις. Οδηγίες Χρήσης

Η χρήση του πυργίσκου είναι αρκετά απλή, εφόσον τα παραπάνω βήματα έχουν γίνει σωστά. 1. Για να ξεκινήσετε την αυτόματη παρακολούθηση, φροντίστε ότι και

οι 2 μπαταρίες είναι συνδεδεμένες και μπορούν να παρέχουν την απαραίτητη ενέργεια για όλη την ώρα που θα λειτουργεί. 2. Συνδέστε το Dev Board στο δίκτυο μέσω wifi. 3. Συνδεθείτε από τον υπολογιστή σας μέσω SSH στο Dev Board. Εάν

δεν έχετε αλλάξει τα στοιχεία, για τον πυργίσκο που υλοποιήθηκε ήδη στα πλαίσια του μαθήματος, τότε:
username = mendel
password = mendel
Εάν ο κωδικός δεν είναι σωστός δοκιμάστε είτε “stathakos” είτε “Stathakos” (χωρίς τα “”). 4. Στην συνέχεια, εκτελέστε την εντολή “cd project-posenet”. Εάν έχετε

φτιάξει δικό σας, τότε μεταβείτε στον φάκελο που βρίσκεται το posenet. 5. Τέλος εκτελέστε την εντολή “python3 pose_camer.py” για να

ξεκινήσει η παρακολούθηση. Συγκεκριμένα για τις δικές μου δοκιμές έτρεχα την εντολή “python3 pose_camera.py --res 480x360 --headless”. Αυτό θέτει την ποιότητα σε 480x360 για να είναι πιο γρήγορο και επίσης με το headless δεν τυπώνει στο video feed τα keypoints κτλ καθώς δεν χρειάζονται. 6. Αν θέλετε να δείτε το video feed, μπορείτε να χρησιμοποιήσετε το

Dev Board σαν Desktop, όπως αναλύθηκε παραπάνω. Σε αυτή την περίπτωση καλό θα ήταν αν αποσυνδέσετε το battery pack, καθώς τα έξτρα καλώδια θα δημιουργήσουν πρόβλημα στην κίνηση του πυργίσκου. 7. Αν συνδεθείτε σαν desktop, τότε εκτελέστε την εντολή “cd ~” 8. Και έπειτα ακολουθήστε τα βήματα 4 και 5 για να τρέξετε το script. Αν θέλετε να δείτε πως φαίνονται τα keypoints μην βάλετε την

παράμετρο “--headless”. Ακόμα αν και η κάμερα και η οθόνη κοιτάνε προς το μέρος σας, φροντίστε να χρησιμοποιήσετε την παράμετρο “--mirror”.

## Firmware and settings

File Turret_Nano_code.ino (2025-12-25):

#include <Arduino.h>
#include <Servo.h>
#include <A4988.h>


Servo laserServo;

#define MOTOR_STEPS 200       // 1.8° per step = 200 steps/rev
#define stepPin 4  // D4 -> STEP
#define direPin 3  // D3 -> DIR
#define RPM 10


float servoPos = 0;
float servoAngle = 40;
float servoGetter = 0;
float stepperPos = 0;
float stepperPosPrev = 0;
int seperate = 0;
String coord;
float Kpx = 0.1; // P like controller, delay the move to reduce jittering
float Kpy = 0.4; // P like controller, delay the move to reduce jittering


A4988 stepper(MOTOR_STEPS, direPin, stepPin);

void setup() {
  laserServo.attach(2); // use D2
  Serial.begin(9600);
  laserServo.write(140); // center position


  stepper.begin(RPM);
  stepper.setMicrostep(1);  // Set to 1 for full-step mode (adjust if using MS1–MS3)


}

void loop() {

  if(Serial.available()){
    // Seperating the Serial input
    coord = Serial.readStringUntil('\n');
    seperate = coord.indexOf(',');

    if(seperate > 0){
      stepperPos = coord.substring(0,seperate).toInt();
      servoGetter = coord.substring(seperate + 1).toInt();

      servoAngle -= Kpy*servoGetter; // Apply the P controller logic

      servoAngle = max(0, min(75, servoAngle)); // constrain the angle betqeen 0 and 75 deg

      servoPos = 180 - servoAngle; // Shift 180 deg, because of the servo orientation

      // This check isn't neccesairy, because we contrained it before
      if(servoPos <= 180 && servoPos >= 0){
        laserServo.write(servoPos); // Move the servo
      }

      // It only does steps between 4 and 50, because of the jittering
      // Furthermore by experiments we conclude that deviding the input by 1.8 to get steps has liitle impact so we leave it as it is
      if(abs(stepperPos) > 4 && abs(stepperPos) <= 50){
        stepperPos = Kpx*stepperPos; // Apply the P controller logic
        stepper.move(stepperPos); // Move the servo
      }
    }
  }
}

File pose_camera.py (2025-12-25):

# Copyright 2019 Google LLC
#
# Licensed under the Apache License, Version 2.0 (the "License");
# you may not use this file except in compliance with the License.
# You may obtain a copy of the License at
#
#     https://www.apache.org/licenses/LICENSE-2.0
#
# Unless required by applicable law or agreed to in writing, software
# distributed under the License is distributed on an "AS IS" BASIS,
# WITHOUT WARRANTIES OR CONDITIONS OF ANY KIND, either express or implied.
# See the License for the specific language governing permissions and
# limitations under the License.

import argparse
import collections
from functools import partial
import re
import time

import numpy as np
from PIL import Image
import svgwrite
import gstreamer
import math

from pose_engine import PoseEngine
from pose_engine import KeypointType

import serial
ser = serial.Serial('/dev/ttyCH341USB0', 9600)


# Global variable for tracking
tracked_face = None
switch_threshold = 1.4  # 40% larger to trigger switch

last_send_time = 0
send_interval = 0.1  # seconds 
headless_flag = False


EDGES = (
    (KeypointType.NOSE, KeypointType.LEFT_EYE),
    (KeypointType.NOSE, KeypointType.RIGHT_EYE),
    (KeypointType.NOSE, KeypointType.LEFT_EAR),
    (KeypointType.NOSE, KeypointType.RIGHT_EAR),
    (KeypointType.LEFT_EAR, KeypointType.LEFT_EYE),
    (KeypointType.RIGHT_EAR, KeypointType.RIGHT_EYE),
    (KeypointType.LEFT_EYE, KeypointType.RIGHT_EYE),
    (KeypointType.LEFT_SHOULDER, KeypointType.RIGHT_SHOULDER),
    (KeypointType.LEFT_SHOULDER, KeypointType.LEFT_ELBOW),
    (KeypointType.LEFT_SHOULDER, KeypointType.LEFT_HIP),
    (KeypointType.RIGHT_SHOULDER, KeypointType.RIGHT_ELBOW),
    (KeypointType.RIGHT_SHOULDER, KeypointType.RIGHT_HIP),
    (KeypointType.LEFT_ELBOW, KeypointType.LEFT_WRIST),
    (KeypointType.RIGHT_ELBOW, KeypointType.RIGHT_WRIST),
    (KeypointType.LEFT_HIP, KeypointType.RIGHT_HIP),
    (KeypointType.LEFT_HIP, KeypointType.LEFT_KNEE),
    (KeypointType.RIGHT_HIP, KeypointType.RIGHT_KNEE),
    (KeypointType.LEFT_KNEE, KeypointType.LEFT_ANKLE),
    (KeypointType.RIGHT_KNEE, KeypointType.RIGHT_ANKLE),
)


def shadow_text(dwg, x, y, text, font_size=16):
    dwg.add(dwg.text(text, insert=(x + 1, y + 1), fill='black',
                     font_size=font_size, style='font-family:sans-serif'))
    dwg.add(dwg.text(text, insert=(x, y), fill='white',
                     font_size=font_size, style='font-family:sans-serif'))


def draw_pose(dwg, pose, src_size, inference_box, color='yellow', threshold=0.2):
    box_x, box_y, box_w, box_h = inference_box
    scale_x, scale_y = src_size[0] / box_w, src_size[1] / box_h
    xys = {}
    for label, keypoint in pose.keypoints.items():
        if keypoint.score < threshold: continue
        # Offset and scale to source coordinate space.
        kp_x = int((keypoint.point[0] - box_x) * scale_x)
        kp_y = int((keypoint.point[1] - box_y) * scale_y)

        xys[label] = (kp_x, kp_y)
        dwg.add(dwg.circle(center=(int(kp_x), int(kp_y)), r=5,
                           fill='cyan', fill_opacity=keypoint.score, stroke=color))

    for a, b in EDGES:
        if a not in xys or b not in xys: continue
        ax, ay = xys[a]
        bx, by = xys[b]
        dwg.add(dwg.line(start=(ax, ay), end=(bx, by), stroke=color, stroke_width=2))


def avg_fps_counter(window_size):
    window = collections.deque(maxlen=window_size)
    prev = time.monotonic()
    yield 0.0  # First fps value.

    while True:
        curr = time.monotonic()
        window.append(curr - prev)
        prev = curr
        yield len(window) / sum(window)


def run(inf_callback, render_callback):
    global headless_flag
    
    parser = argparse.ArgumentParser(formatter_class=argparse.ArgumentDefaultsHelpFormatter)
    parser.add_argument('--mirror', help='flip video horizontally', action='store_true')
    parser.add_argument('--model', help='.tflite model path.', required=False)
    parser.add_argument('--res', help='Resolution', default='640x480',
                        choices=['480x360', '640x480', '1280x720'])
    parser.add_argument('--videosrc', help='Which video source to use', default='/dev/video1')
    parser.add_argument('--h264', help='Use video/x-h264 input', action='store_true')
    parser.add_argument('--jpeg', help='Use image/jpeg input', action='store_true')
    parser.add_argument('--headless', help='Disable display output', action='store_true')

    args = parser.parse_args()

    default_model = 'models/mobilenet/posenet_mobilenet_v1_075_%d_%d_quant_decoder_edgetpu.tflite'
    if args.res == '480x360':
        src_size = (640, 480)
        appsink_size = (480, 360)
        model = args.model or default_model % (353, 481)
    elif args.res == '640x480':
        src_size = (640, 480)
        appsink_size = (640, 480)
        model = args.model or default_model % (481, 641)
    elif args.res == '1280x720':
        src_size = (1280, 720)
        appsink_size = (1280, 720)
        model = args.model or default_model % (721, 1281)

    if args.headless:
        headless_flag = True

    print('Loading model: ', model)
    engine = PoseEngine(model)
    input_shape = engine.get_input_tensor_shape()
    inference_size = (input_shape[2], input_shape[1])

    gstreamer.run_pipeline(partial(inf_callback, engine), partial(render_callback, engine),
                           src_size, inference_size,
                           mirror=args.mirror,
                           videosrc=args.videosrc,
                           h264=args.h264,
                           jpeg=args.jpeg
                           )
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
